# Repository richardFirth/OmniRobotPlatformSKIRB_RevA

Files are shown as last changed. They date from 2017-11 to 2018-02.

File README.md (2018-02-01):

# OmniRobotPlatformSKIRB_RevA  
Documentation of my Omni robot platform.

**work in progress, i am still adding stuff as of Jan 18**

The robot is designed to be modular and is based around a 3D Printed/Laser cut chassis.
This has a motor control board that connects to the battery and switch.
The motor control board has a socket that can accept different boards that are plugged in.

Folders:
**Chassis_Assembly**: Documentation of physical assembly of Omnibot platform

**MotorBoard_Assemly**: Documentation of motor driver Board

**XBeeControl_Module**: Documentation of a board to control the omnibot via sparkfun joystick

Different modules can be attached to the shield for control via different methods.  

**CAD Model:**  https://grabcad.com/library/omni-robot-platform-skirb_reva-1  

**Joystick Code and Case:** https://github.com/richardFirth/WirelessJoystick  

Order PCB's in Model  
**Motor Control Board:** https://oshpark.com/shared_projects/BiVYTwTP  
**XBee plugonboard** https://oshpark.com/shared_projects/E1SlzLHo  
**Xbee Board:** https://oshpark.com/shared_projects/hA4cGipD  
**MotorClip** https://oshpark.com/shared_projects/modA4HzY (Need 4)  
**MotorBackplate** https://oshpark.com/shared_projects/eEKy6Eoc (Need 4, optional)

(you need one of each to build the Robot)  

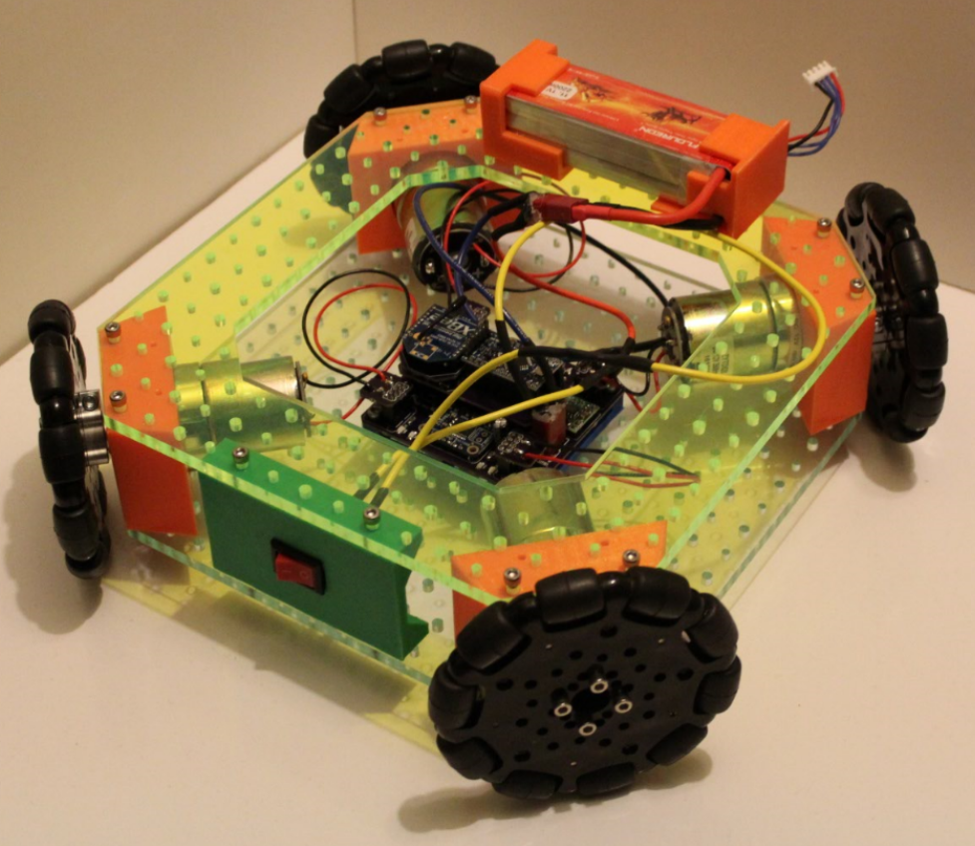
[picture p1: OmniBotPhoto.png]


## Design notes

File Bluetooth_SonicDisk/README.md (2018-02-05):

# Bluetooth Sonic Disk

This is for a version of the omnibot that uses the sonic disk https://github.com/richardFirth/sonicdisc on top of it to display the surroundings
using bluetooth.

Sonic Disk -> https://github.com/richardFirth/sonicdisc / https://platis.solutions/blog/2017/08/27/sonicdisc-360-ultrasonic-scanner/

Youtube video: https://www.youtube.com/watch?v=5h7yqy7BErE (crappy video - if there is interest I'll make a better one)

**CAD Model:**  https://grabcad.com/library/sonic-disk-mount-1   

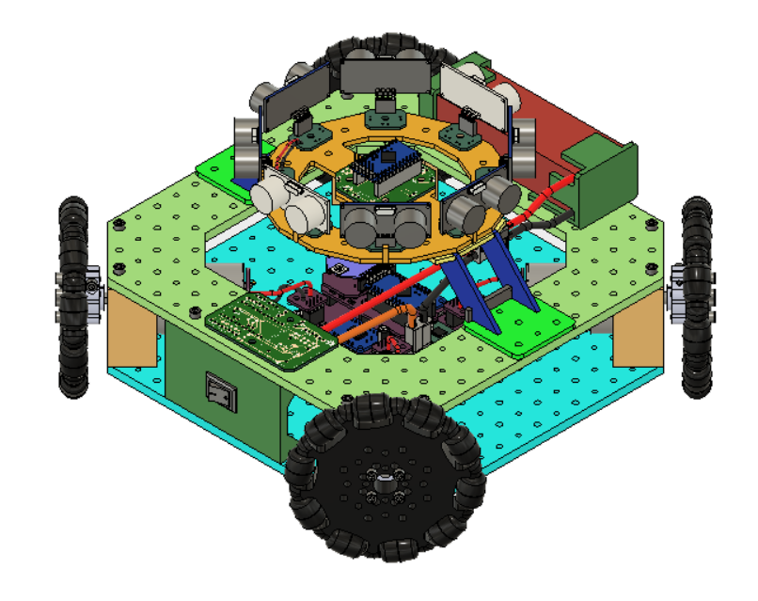
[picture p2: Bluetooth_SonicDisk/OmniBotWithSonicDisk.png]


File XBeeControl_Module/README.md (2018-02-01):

# XBeeControl_Module

Plug-In Module for control with xbee joystick 
https://github.com/richardFirth/WirelessJoystick 

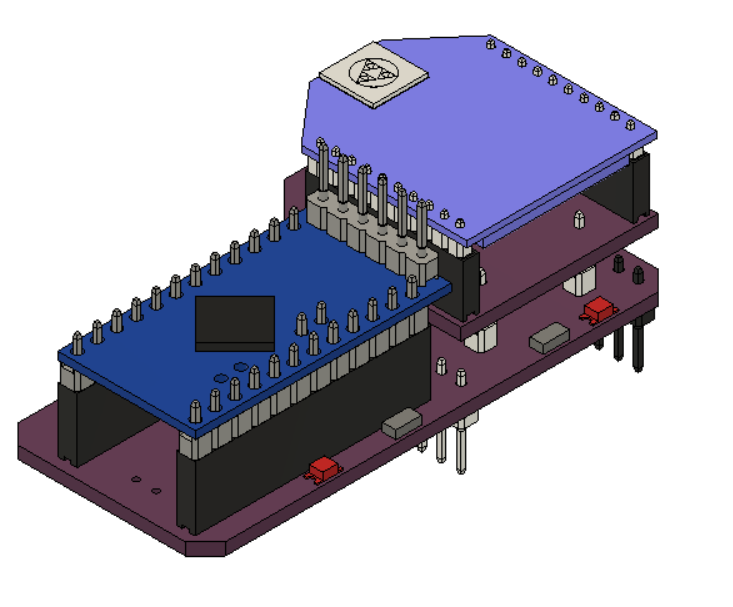
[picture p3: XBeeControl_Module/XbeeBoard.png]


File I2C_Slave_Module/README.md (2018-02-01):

# I2C Slave Module

This module has the arduino act as an I2C Slave that passes commands down to the omnibots motors.
it also exposes the power out portion of the motor board so more stuff can be attached upstream.

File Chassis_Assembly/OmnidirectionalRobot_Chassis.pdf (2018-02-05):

# Omni Robot Platform

## Richard Firth 1/25/18

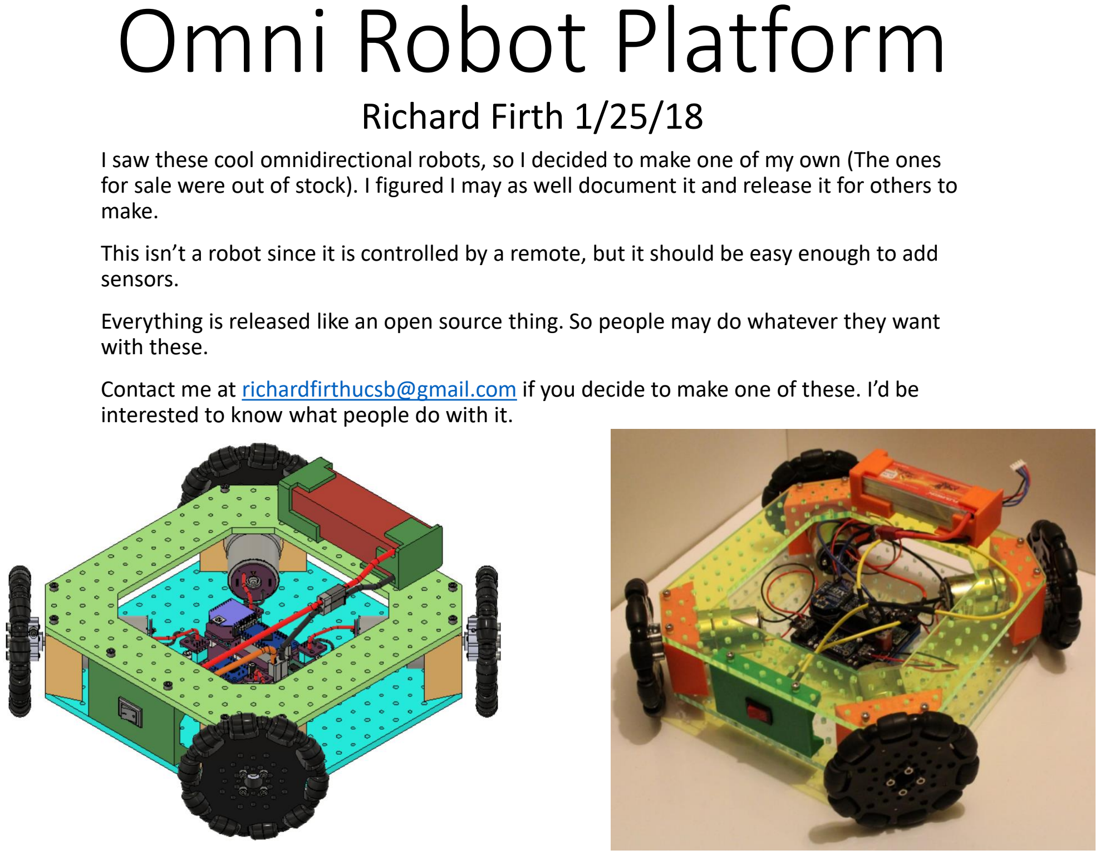
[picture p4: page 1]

I saw these cool omnidirectional robots, so I decided to make one of my own (The ones for sale were out of stock). I figured I may as well document it and release it for others to make.

This isn’t a robot since it is controlled by a remote, but it should be easy enough to add sensors.

Everything is released like an open source thing. So people may do whatever they want with these.

Contact me at richardfirthucsb@gmail.com if you decide to make one of these. I’d be interested to know what people do with it.

# Goal / Contents

- Electronics/soldering
- Arduino Programming
- Knowledge of Xbees
- 3D printing
- ~$450 + equipment

# Resources:

# Prerequisites:

Github: https://github.com/richardFirth/OmniRobotPlatformSKIRB_RevA CAD Files: https://grabcad.com/library/omni-robot-platform-skirb_reva-1

- Provide high level instructions on how to construct the robot platform
- List the parts used in constructing the robot platform
- Go over the design/engineering of the thing, so that people can understand how it was designed & constructed

# Price estimate: ~$200

# - Each wheel assy ~$30 ($120 for wheels) - LiPO battery $16 - Misc screws, wire ect $20 - 3D printed parts, laser cut parts $30

# 3D Printed Parts Index

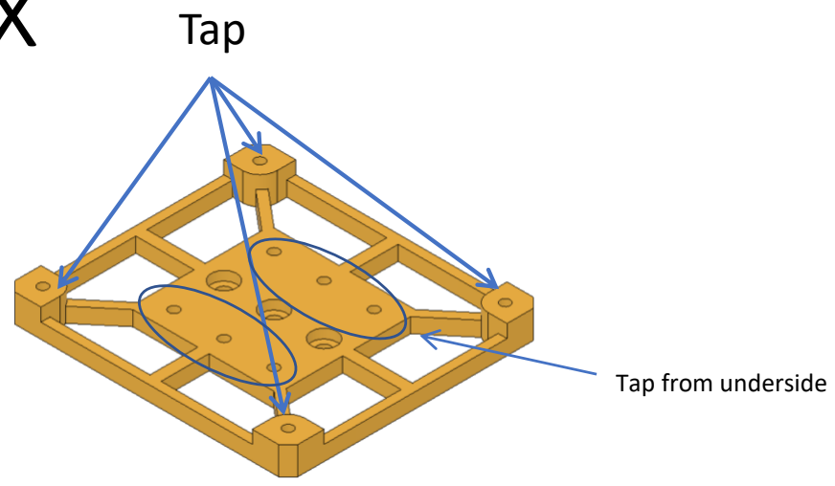
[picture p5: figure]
Tap; Tap from underside
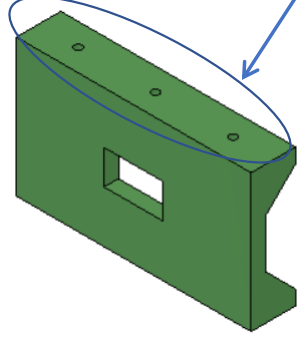
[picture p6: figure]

SwitchHolder

Standoff_Omni

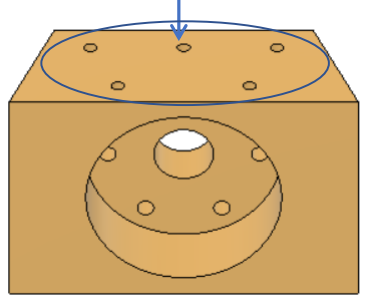
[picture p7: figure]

MotorHolderD (X4)

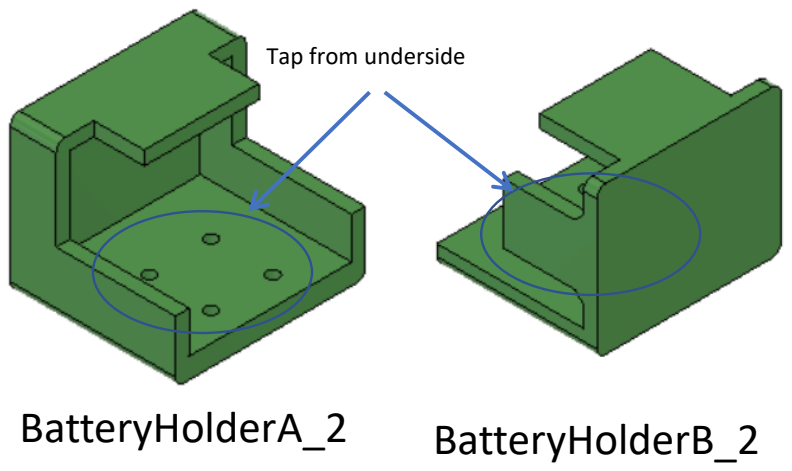
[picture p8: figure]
BatteryHolderA_2; BatteryHolderB_2; Tap from underside

- Holes match the spacing for attaching stuff bought on servocity.com
- Thread holes using a 6-32 tap
- https://www.mcmaster.com/#2548a12/=1a34129
- https://www.mcmaster.com/#27175a114/=1a340o6

Tap both top and bottom

Tap both top and bottom

# Wheels

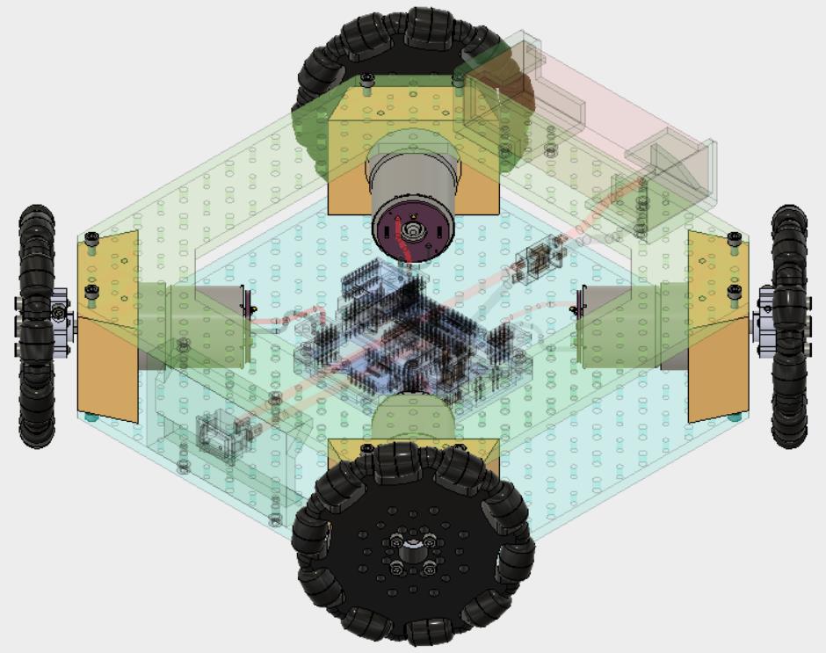
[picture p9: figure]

# Wheel Assembly (4 needed)

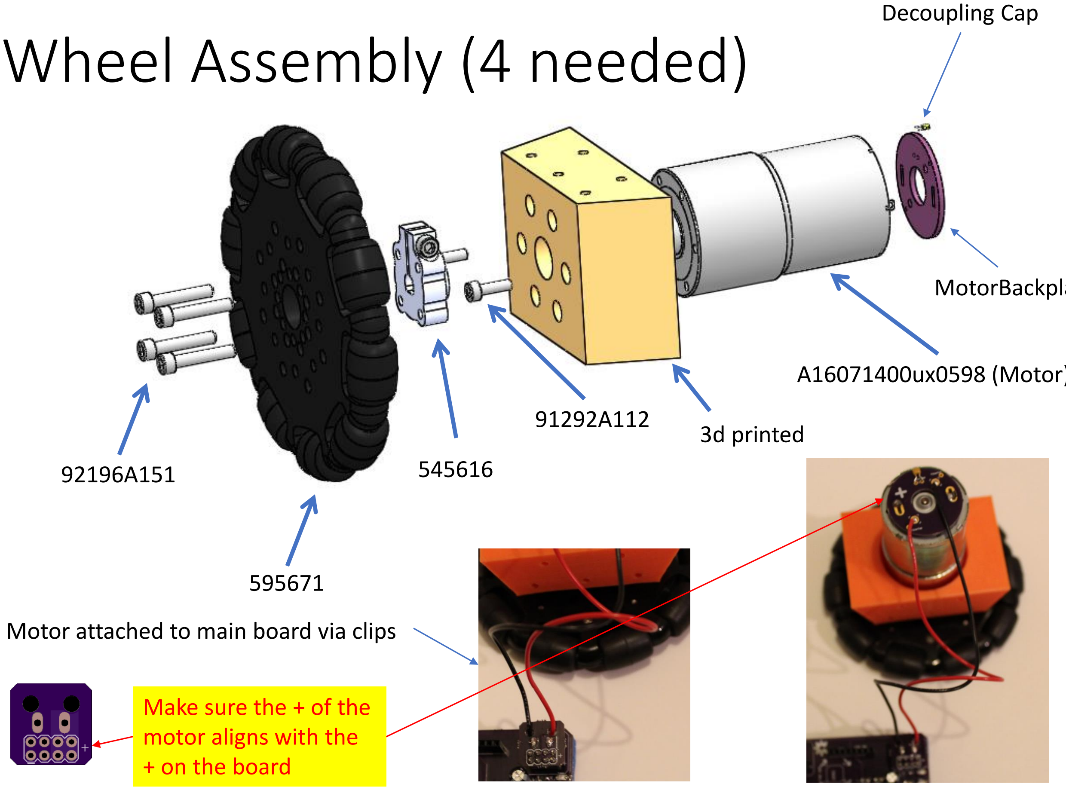
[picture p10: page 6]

A16071400ux0598 (Motor)

92196A151

91292A112

595671

545616

Decoupling Cap

Motor attached to main board via clips

3d printed

MotorBackplate

Make sure the + of the
motor aligns with the
+ on the board

Part # | Part | Pic | Source
92196A151 | 18-8 Stainless Steel Socket Head Screw 6-32 Thread Size, 3/4" Long | | https://www.mcmaster.com/#92196A151/
92196A146 | 18-8 Stainless Steel Socket Head Screw, 6-32 Thread Size, 3/8" Long | | https://www.mcmaster.com/#92196A146/
91292A112 | 8-8 Stainless Steel Socket Head Screw M3 x 0.5 mm Thread, 8 mm Long | | https://www.mcmaster.com/#91292A112/
Part # | Description | Pic | Source
ZGA37RG31 (Gearbox) a16071400ux0598 (Uxcell P/N) | 12V 100 RPM DC Motor | | https://www.amazon.com/gp/product/B01KTZXZ1G/
545616 | Face Tapped Clamping Hubs, 0.770" Pattern (6mm) | | https://www.servocity.com/770-clamping-hubs#348=98
595671 | 4" Omni Wheel | | https://www.servocity.com/4-omni-wheel
0.1 uF Ceramic Capacitor | 0.1 uF Ceramic Capacitor | | https://www.amazon.com/gp/product/B01N3L8IE1
MotorBackplate | MotorBackplate | | https://oshpark.com/shared_projects/eEKy6Eoc
MotorClip | MotorClip | | https://oshpark.com/shared_projects/modA4HzY
Wire | Wire | | https://www.amazon.com/gp/product/B01180QKJ0/

# Bill of materials – Wheel Assemblies (Need 4)

# Body

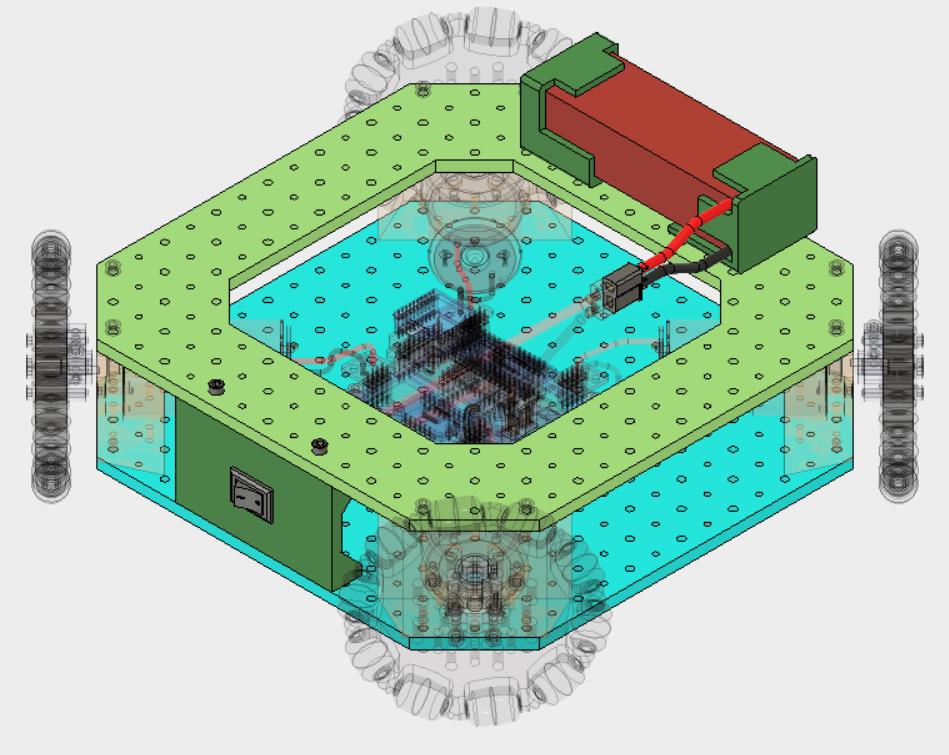
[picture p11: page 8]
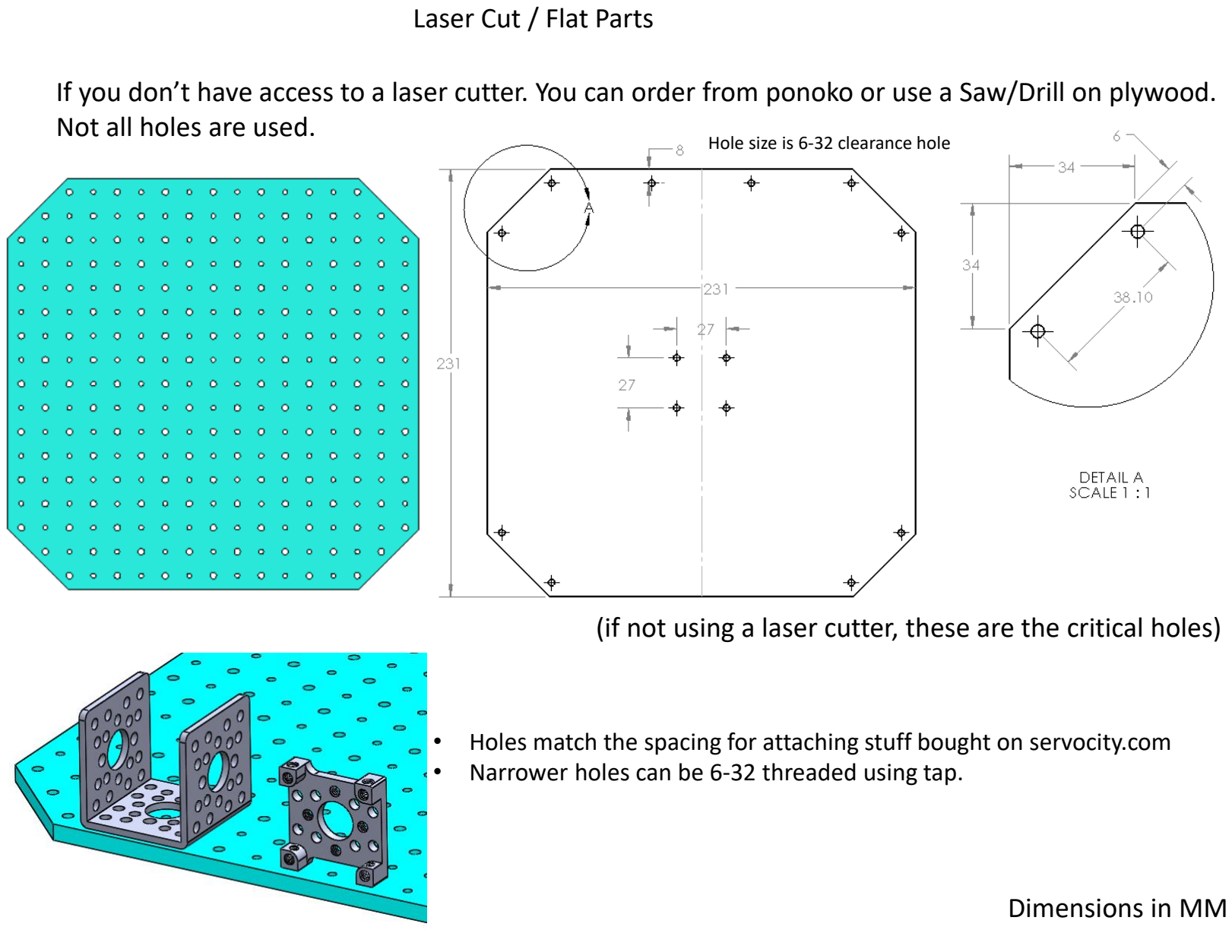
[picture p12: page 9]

Laser Cut / Flat Parts

If you don’t have access to a laser cutter. You can order from ponoko or use a Saw/Drill on plywood. Not all holes are used.

Dimensions in MM

(if not using a laser cutter, these are the critical holes)

Hole size is 6-32 clearance hole

- Holes match the spacing for attaching stuff bought on servocity.com
- Narrower holes can be 6-32 threaded using tap.

If you don’t have access to a laser cutter. You can order from ponoko or use a Saw/Drill on plywood. Extra holes are to support future stuff you might add.

Laser Cut / Flat Parts

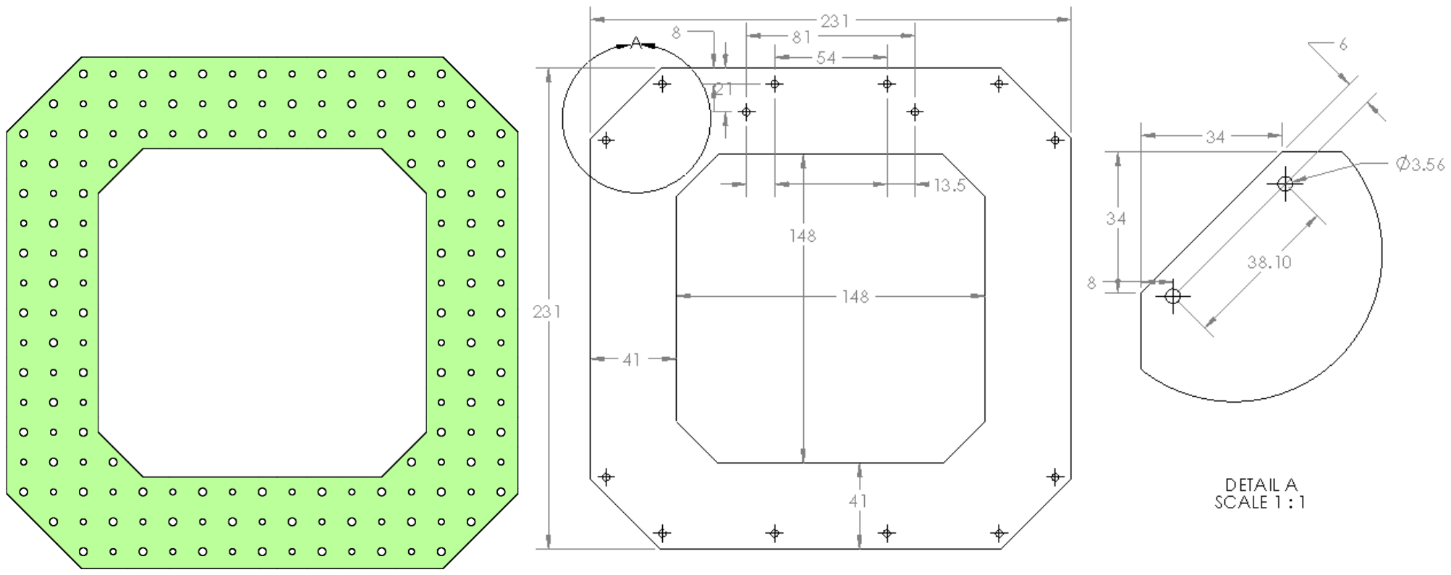
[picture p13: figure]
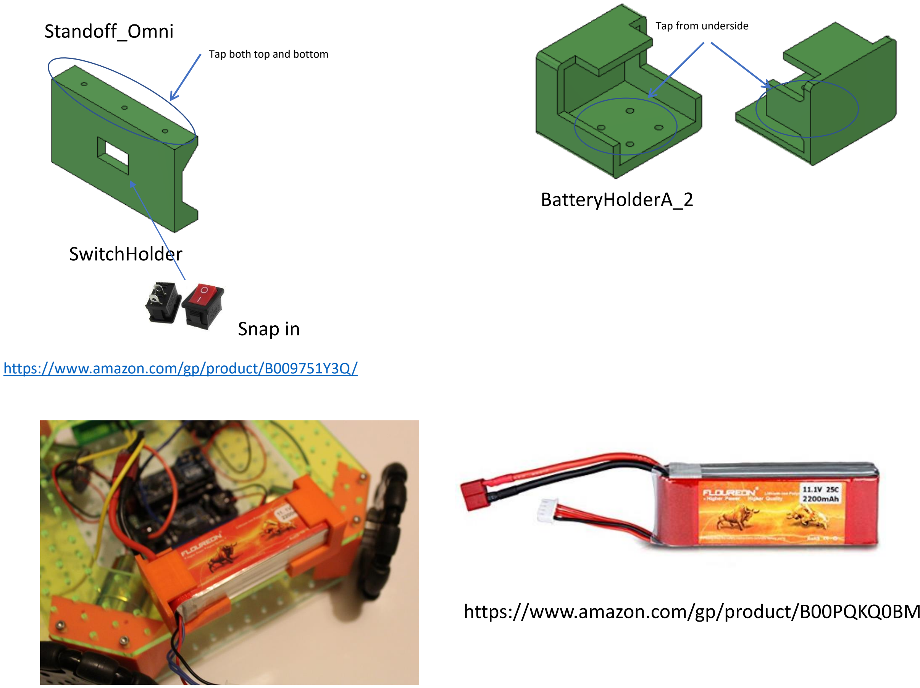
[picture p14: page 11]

SwitchHolder

Standoff_Omni

Tap both top and bottom

https://www.amazon.com/gp/product/B00PQKQ0BM

BatteryHolderA_2

Tap from underside

https://www.amazon.com/gp/product/B009751Y3Q/

Snap in

Wiring

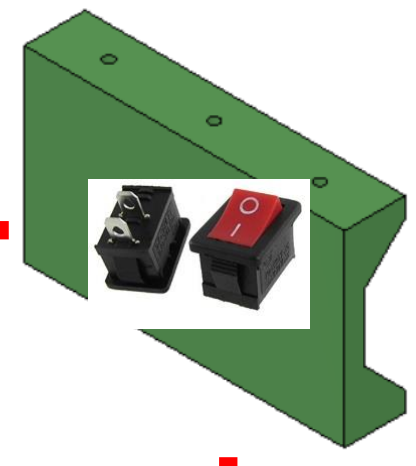
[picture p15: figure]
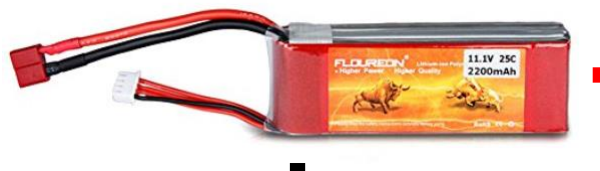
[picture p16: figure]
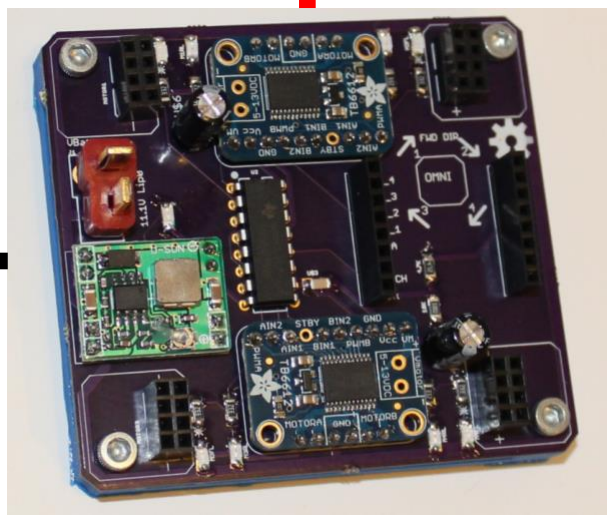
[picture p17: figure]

# Circuit board Holder

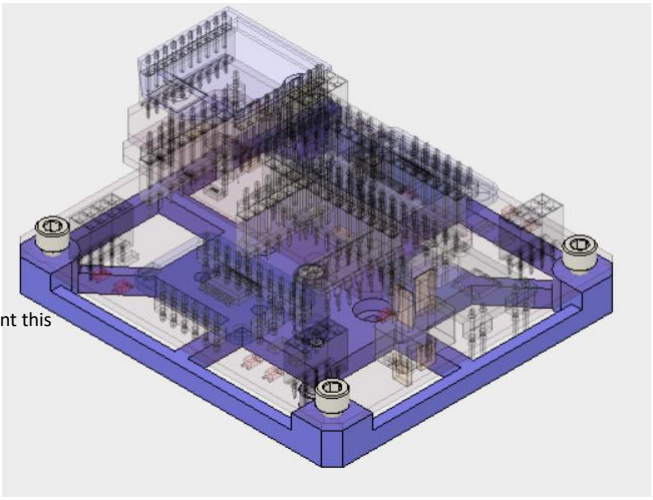
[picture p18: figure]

3d Print this

MotorClip -> https://oshpark.com/shared_projects/modA4HzY (need 4)
MotorBackplate -> https://oshpark.com/shared_projects/eEKy6Eoc (need 4, optional part)

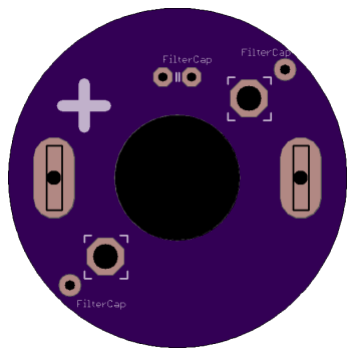
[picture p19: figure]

MotorBackplate

Not to Scale!

MotorClip

# Printed Circuit Boards

# Design Notes - Mechanical

- For the frame and wheels, the materials were chosen based on the fact I have access to a laser cutter and 3D printer and am familiar with them
- Wheels, hubs, screw sizes ect were chosen to match stuff off ServoCity, because I have a bunch of their stuff already, and the hole pattern lets me attach actobotics stuff to the robot
- The motor was the first guess, and worked so I didn’t try others. Of the choices available 100 RPM seemed a good place to start. (https://www.amazon.com/gp/product/B01KTZXZ1G/) and they don’t use a lot of current (around 0.5 amp when resisted according to an ad hoc test – I used a benchtop power supply and grabbed the wheel physically and resisted it while looking at the current)
- The battery was the second of a two pack bought for another project, but works well here.
- I didn’t really think about cost as a thing since this is a one off for learning purposes

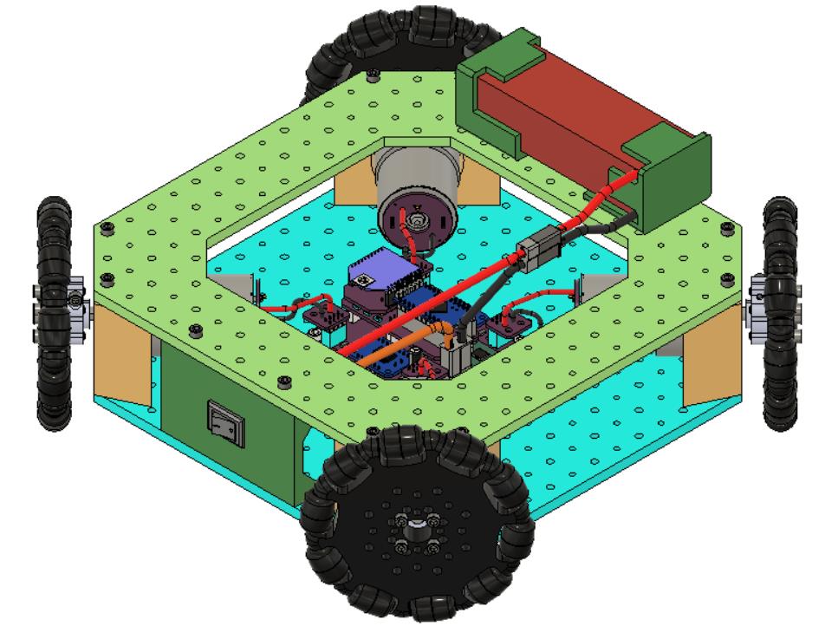
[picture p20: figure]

Forward sense of each motor should cause clockwise rotation of robot (VCC to + of motor, GND to -)

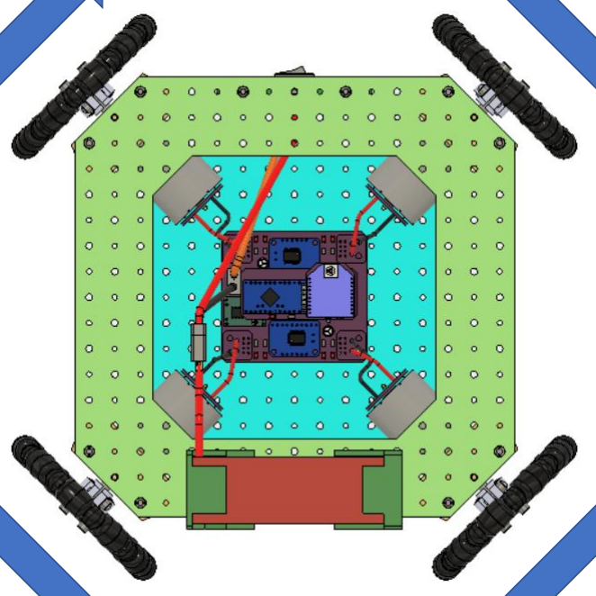
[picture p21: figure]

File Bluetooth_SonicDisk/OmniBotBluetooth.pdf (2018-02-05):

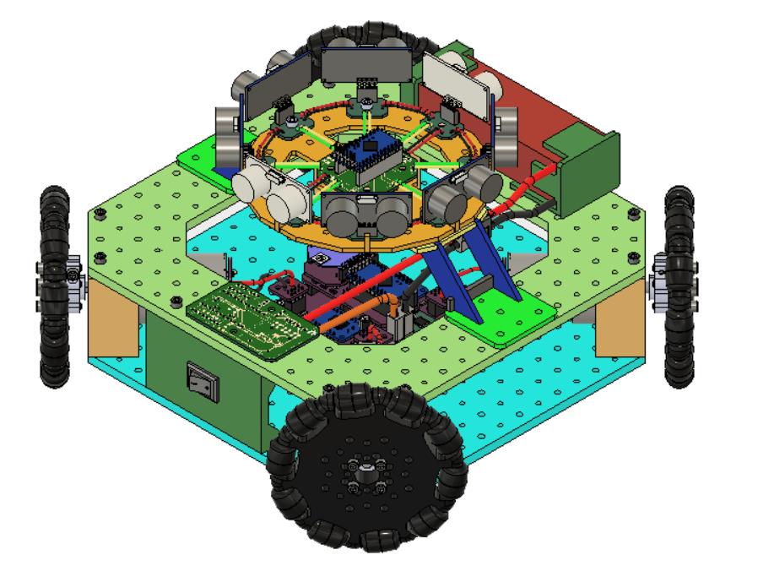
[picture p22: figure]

Uses Three Arduino pro minis.

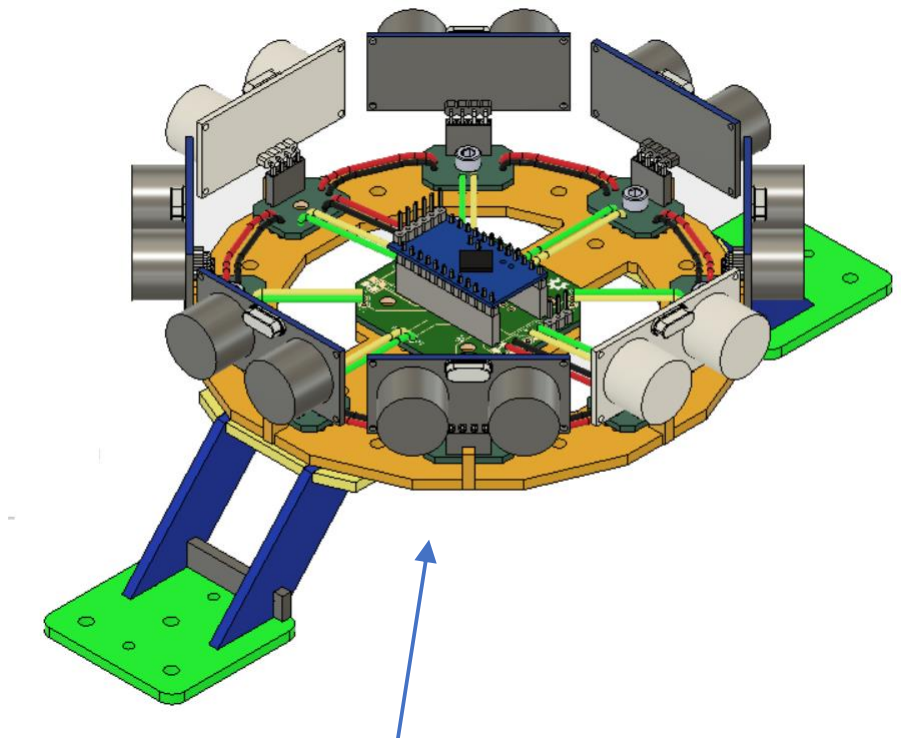
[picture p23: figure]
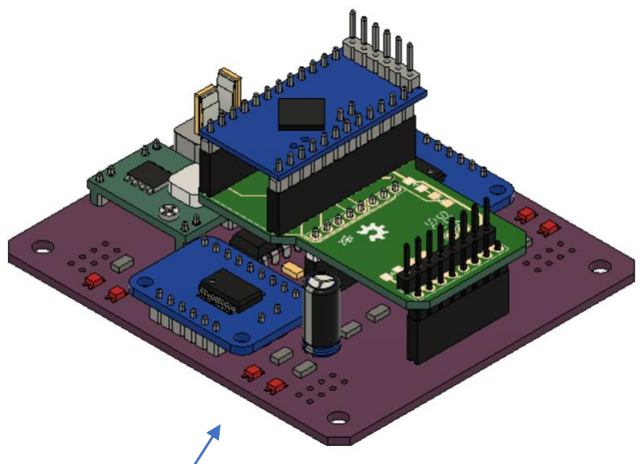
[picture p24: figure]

Arduino 2 – Sonic Disc
Code:
https://github.com/richardFirth/sonicdisc/tree/master/firmware/SonicDisc (is same as https://github.com/platisd/sonicdisc/tree/master/firmware )

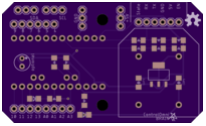
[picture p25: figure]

Arduino 1 – Sonic Disc
Code:
https://github.com/richardFirth/OmniRobotPlatformSKIRB_RevA/tree/master/Bluetooth_SonicDisk/BrainMaster (https://github.com/richardFirth/OmniRobotPlatformSKIRB_RevA/tree/master/Bluetooth_SonicDisk/BrainMaster)

Arduino 3 – Motor Board
Code:
https://github.com/richardFirth/OmniRobotPlatformSKIRB_RevA/tree/master/I2C_Slave_Module/OmniwheelRobot_I2CSlave (https://github.com/richardFirth/OmniRobotPlatformSKIRB_RevA/tree/master/I2C_Slave_Module/OmniwheelRobot_I2CSlave)


## SDA SCL


## SDA SCL

## PIN 2


## INT PIN

## Power & GND

## Power & GND

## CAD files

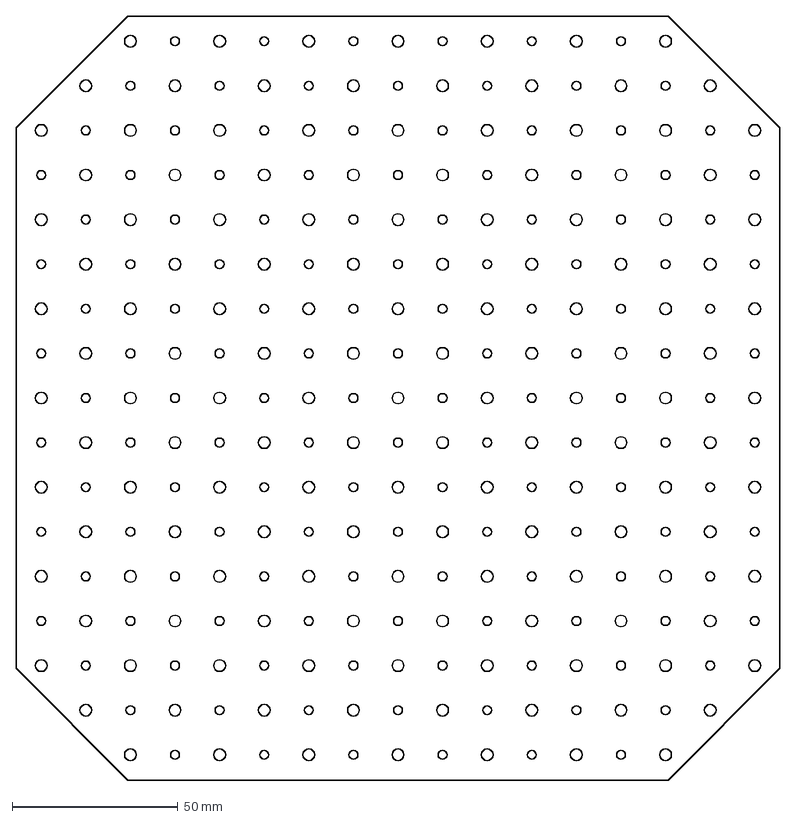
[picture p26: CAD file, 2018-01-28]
Chassis_Assembly/DXF/LowerPlate.dxf
230.8 x 230.8 mm

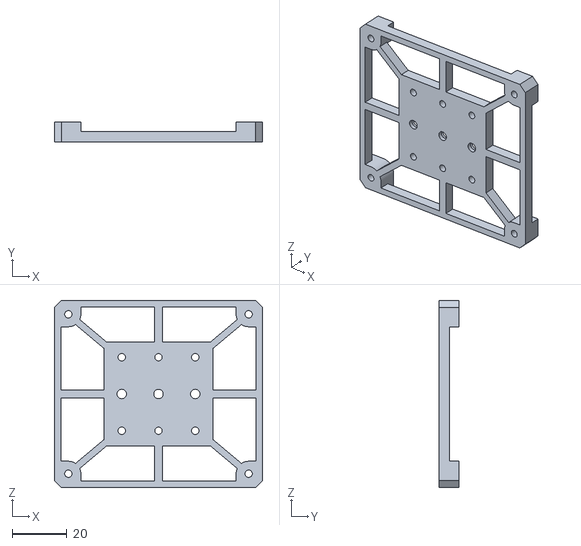
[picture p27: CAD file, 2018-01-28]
Chassis_Assembly/STL/PCB_Holder.stl
76.2 x 7.50 x 68.6

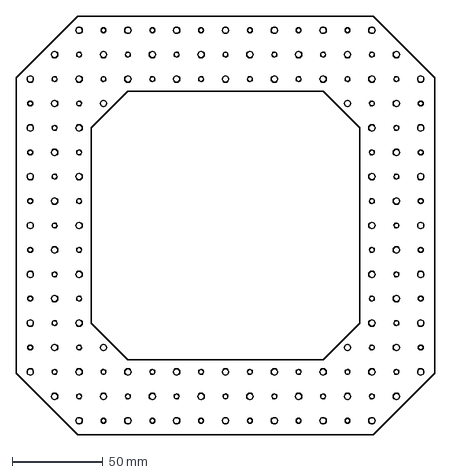
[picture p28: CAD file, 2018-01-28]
Chassis_Assembly/DXF/UpperPlate.dxf
230.8 x 230.8 mm

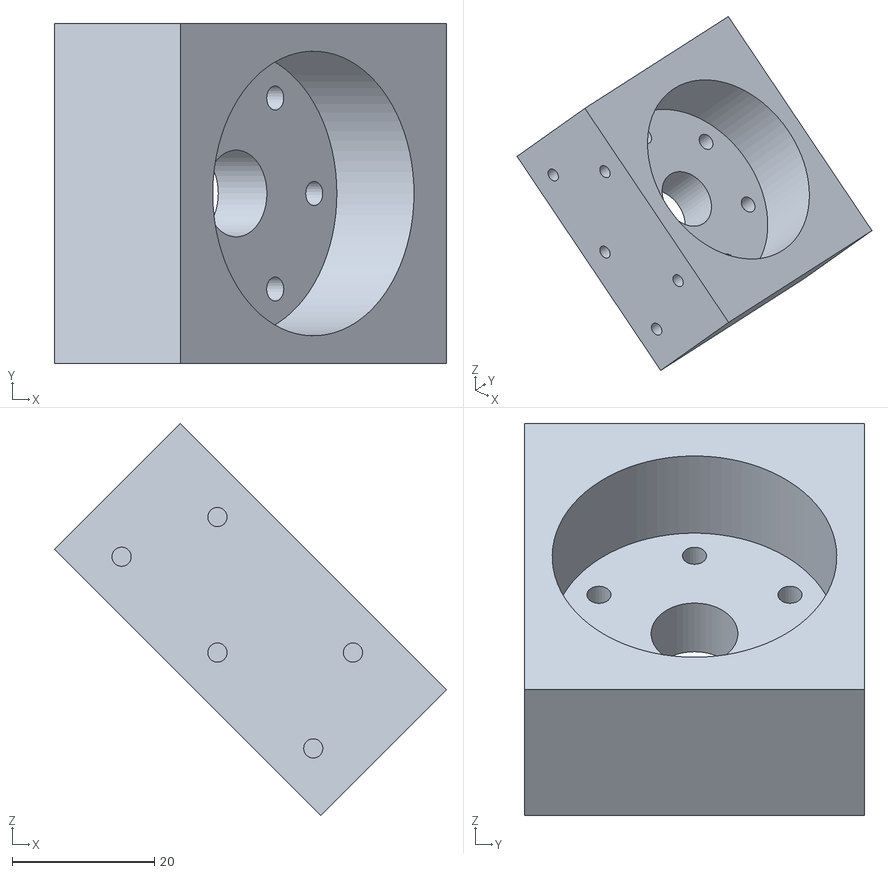
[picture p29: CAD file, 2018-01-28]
Chassis_Assembly/STL/MotorHolderE.stl
55.1 x 47.8 x 55.1

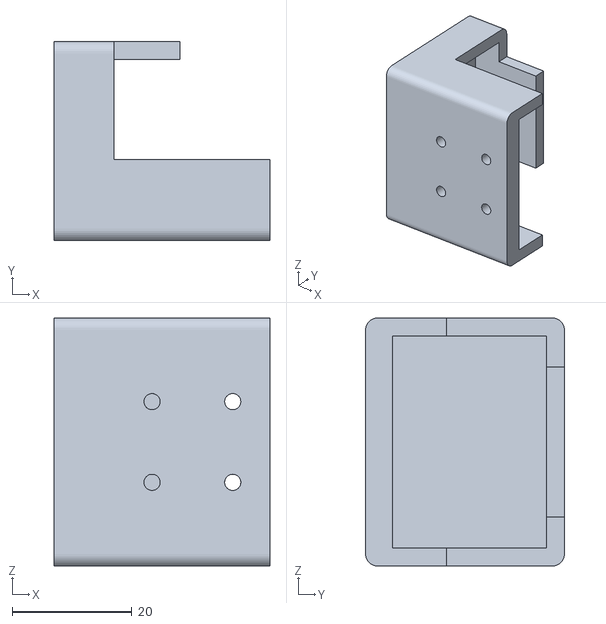
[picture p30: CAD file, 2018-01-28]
Chassis_Assembly/STL/BatteryHolderA_2.stl
36.0 x 33.2 x 41.4

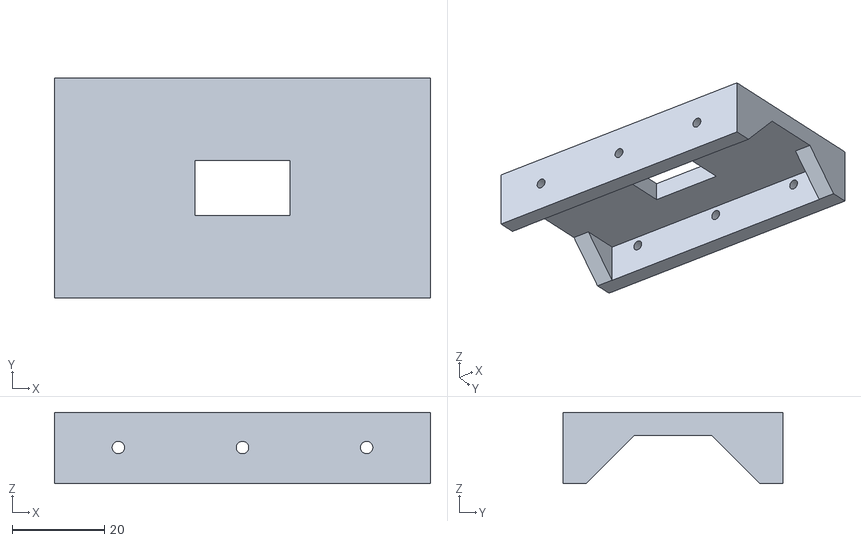
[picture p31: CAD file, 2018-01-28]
Chassis_Assembly/STL/SwitchHolder.stl
81.6 x 47.8 x 15.4

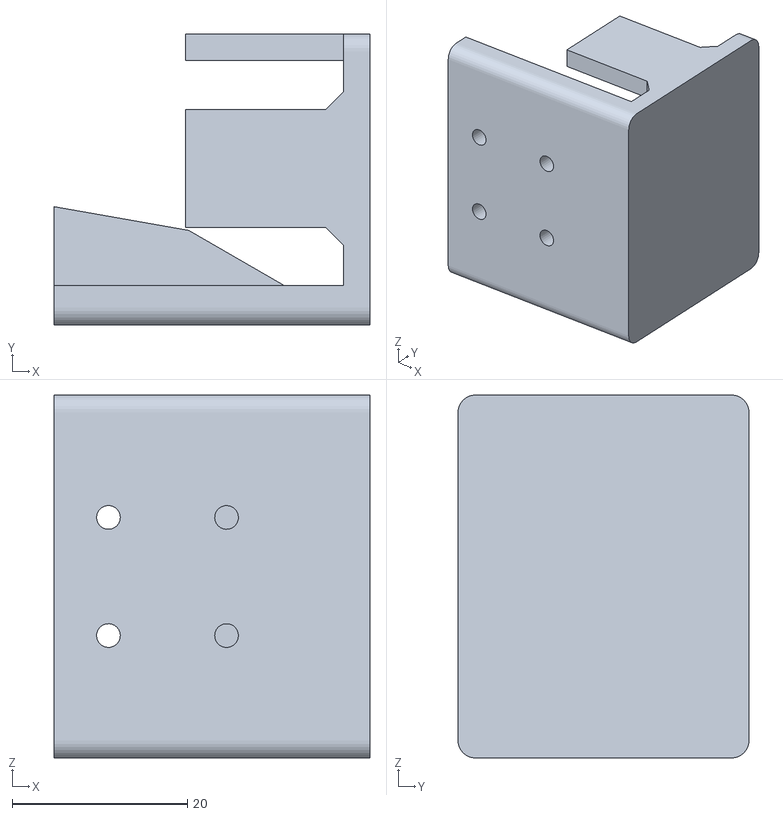
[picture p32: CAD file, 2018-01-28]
Chassis_Assembly/STL/BatteryHolderB_2.stl
36.0 x 33.2 x 41.4

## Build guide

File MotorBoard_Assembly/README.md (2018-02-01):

# Motor Board

Instructions for assembling the motor board.
This is used by each of the modules to control the motors of the omnibot.
It has a common output that can be used by whatever you put above it.

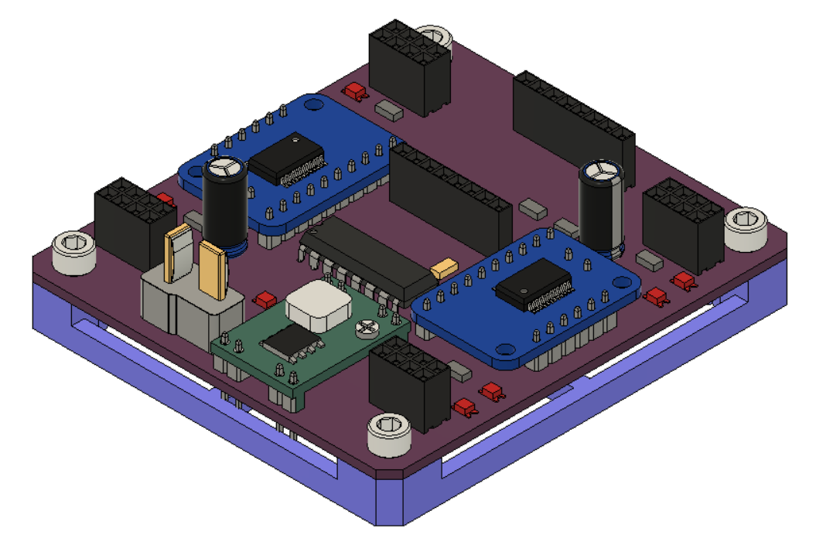
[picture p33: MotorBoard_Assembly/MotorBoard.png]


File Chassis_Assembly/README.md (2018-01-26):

# Chassis Construction  

instructions for construction of physical chassis.
Uses laser cut & 3D Printed components. 

**CAD Model:**  https://grabcad.com/library/omni-robot-platform-skirb_reva-1

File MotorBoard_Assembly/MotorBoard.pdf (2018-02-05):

# Omni Robot Platform

## Richard Firth 11/25/17

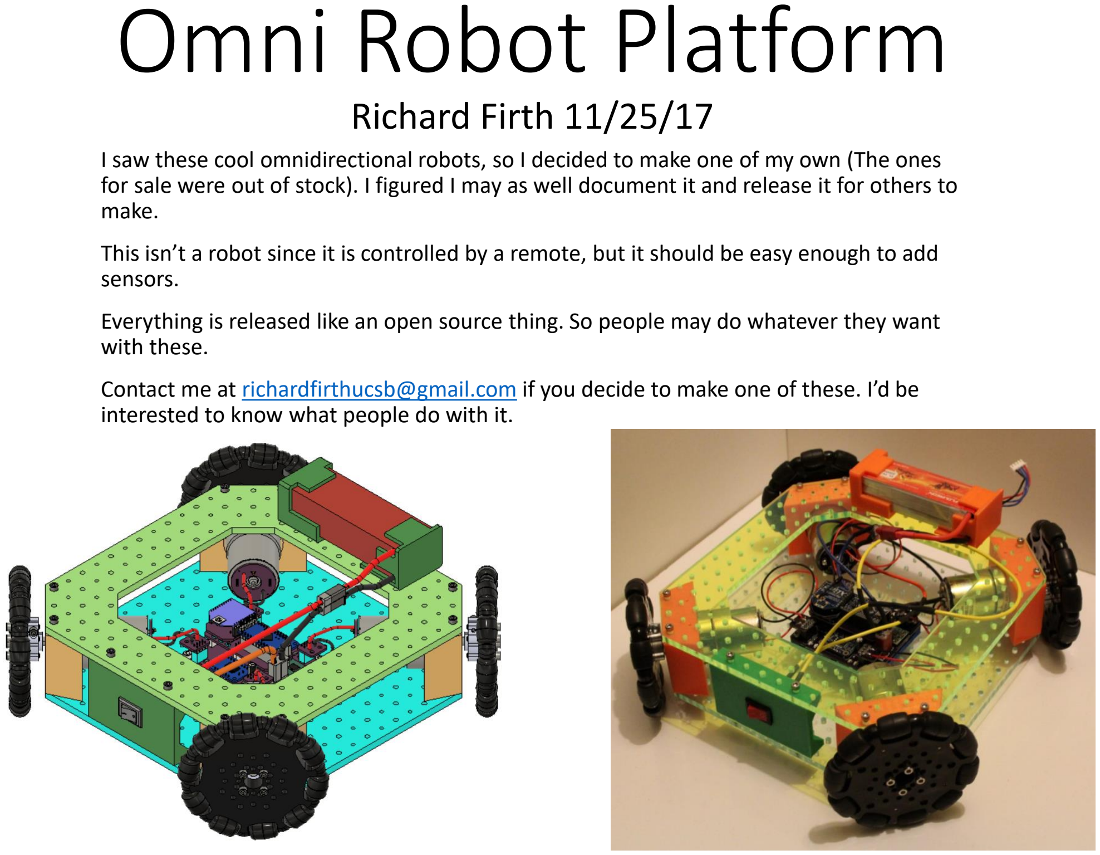
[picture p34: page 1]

I saw these cool omnidirectional robots, so I decided to make one of my own (The ones for sale were out of stock). I figured I may as well document it and release it for others to make.

This isn’t a robot since it is controlled by a remote, but it should be easy enough to add sensors.

Everything is released like an open source thing. So people may do whatever they want with these.

Contact me at richardfirthucsb@gmail.com if you decide to make one of these. I’d be interested to know what people do with it.

# Goal / Contents

- Electronics/soldering
- Arduino Programming

# Resources:

# Prerequisites:

Github: https://github.com/richardFirth/OmniRobotPlatformSKIRB_RevA CAD Files: https://grabcad.com/library/omni-robot-platform-skirb_reva-1

- Provide high level instructions on how to construct the robot platform
- List the parts used in constructing the robot platform
- Go over the design/engineering of the thing, so that people can understand how it was designed & constructed

# Motor control board

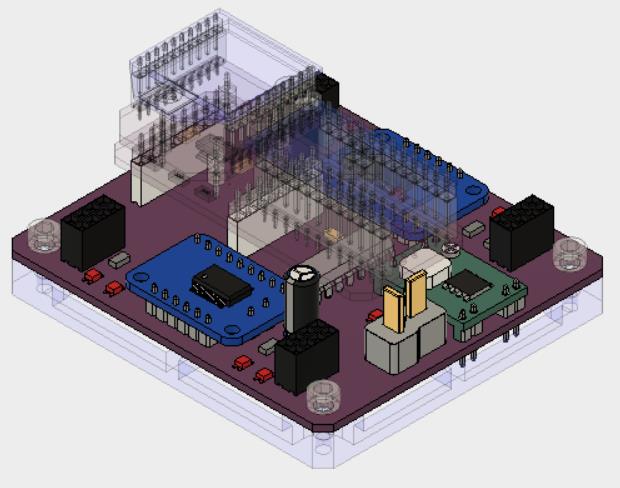
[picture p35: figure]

# OmniMotor_MotorOnly Assembly

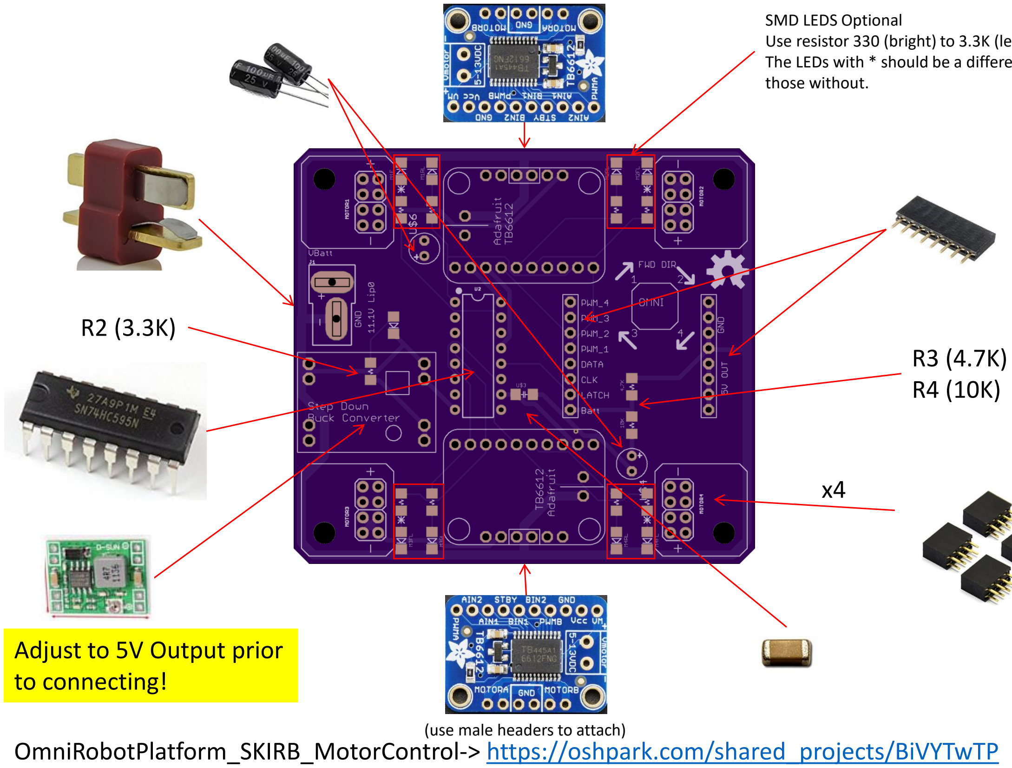
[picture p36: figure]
SMD LEDS Optional; those without.; (use male headers to attach); Adjust to 5V Output prior to connecting!; OmniRobotPlatform_SKIRB_MotorControl-> https://oshpark.com/shared_projects/BiVYTwTP

Use resistor 330 (bright) to 3.3K (less bright) The LEDs with * should be a different color to

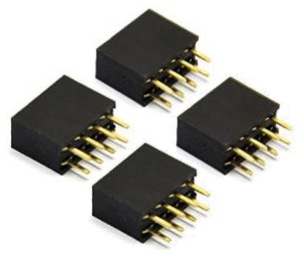
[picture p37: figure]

# OmniMotor_MotorOnly Assembly

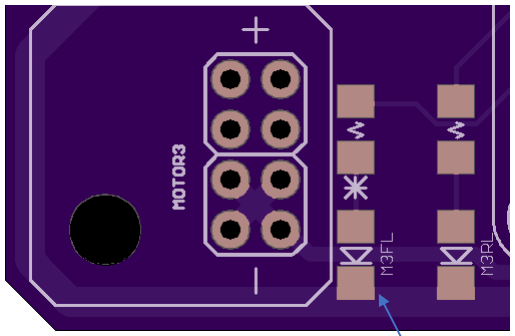
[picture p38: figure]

If you add the SMD LEDS, make the ones with the * all the same color, and the other ones a different color. These indicate ‘forwards’ and ‘backwards’ Use 3.3K resisitors for the SMD LEDS.

# OmniMotor_MotorOnly Assembly

MOTOR 1 | MOTOR 2
MOTOR 3 | MOTOR 4

Part # | Part | Pic | Source
1 | SN74HC595 Shift Register | | https://www.amazon.com/gp/product/B011NA30RK
2 | Adafruit TB6612 1.2A DC/Stepper Motor Driver Breakout Board | | https://www.adafruit.com/product/2448
3 | Icstation Mini DC Voltage Regulator Step Down Buck Converter Power Supply Module 4.5V-28V to 0.8V-20V 3A | | https://www.amazon.com/gp/product/B06Y1ZBY8Q
4 | Plug Connectors Deans Style | | https://www.amazon.com/gp/product/B00S7G4A14
5 | 2.54mm Pitch 2X4 8 Pin Female Double Row Straight Header PCB Connector | | https://www.amazon.com/gp/product/B01IHBCO2K
6 | 100 uF 25 V 612 Electrolytic capacitor | | https://www.amazon.com/gp/product/B01M8QC1E3
7 | 2.54mm Single Row Female Pitch Header Socket Connector PCB 8 Pin Strip | | https://www.amazon.com/gp/product/B00SUXT67M
8 | AVX 0.1uF 50V SMD (Surface Mount) | | https://www.amazon.com/gp/product/B0015A6Z5I
Part Num | Resistor Values (1206 SMT) | Link
R1 | 330 Ohm | https://www.amazon.com/gp/product/B00NQ4JZDA
R2 | 3.3K Ohm | https://www.amazon.com/gp/product/B007V6AQ64
R3 | 4.7K Ohm | https://www.amazon.com/gp/product/B01DKC5BBM
R4 | 10K Ohm | https://www.amazon.com/gp/product/B073RYS2BL

# OmniMotor_MotorOnly BOM

OmniRobotPlatform_SKIRB_MotorControl-> https://oshpark.com/shared_projects/BiVYTwTP

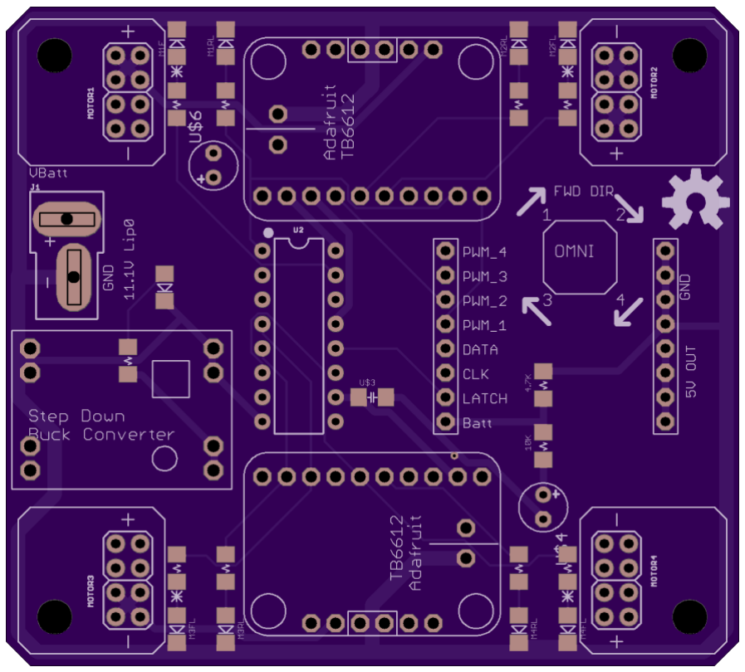
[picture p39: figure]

OmniRobotPlatform_SKIRB_MotorControl

Not to Scale!

# Printed Circuit Boards

# Design Notes - Electrical

- The motor portion was separated from the control portion, since I figured I would be adding sensors and redoing the control portion later
- Shift register used to control the motor drivers, which lets me use 3 pins to control 8 inputs.
- I used the 2X4 female headers at little clips for the motors so it’s easy to attach and detach them.
- SMD lights are there because I just learned to do SMD stuff and wanted to put them everywhere and see stuff.

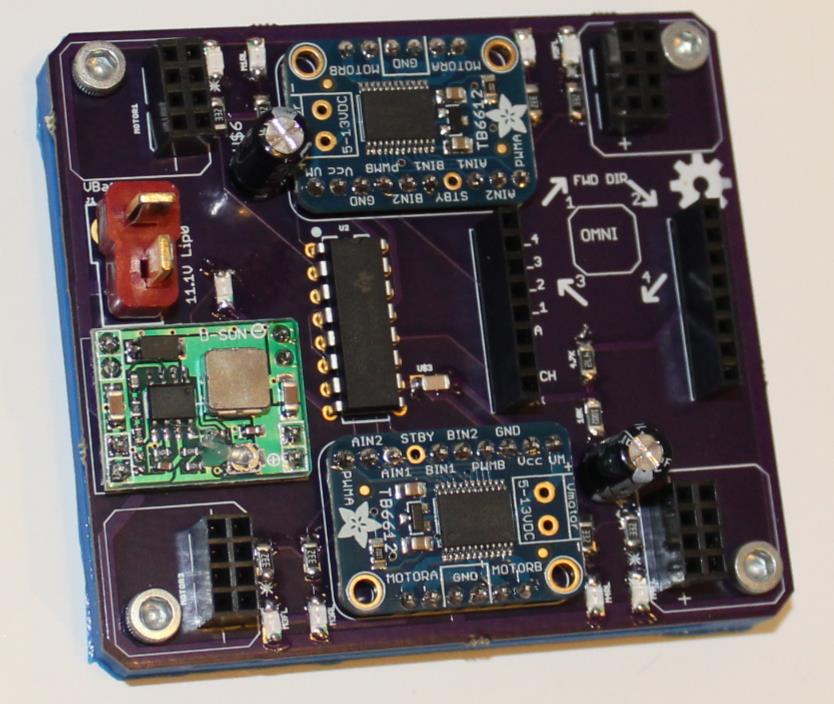
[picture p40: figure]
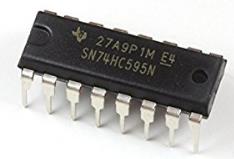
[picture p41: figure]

# Design Notes - Electrical

4 pins connect to ground

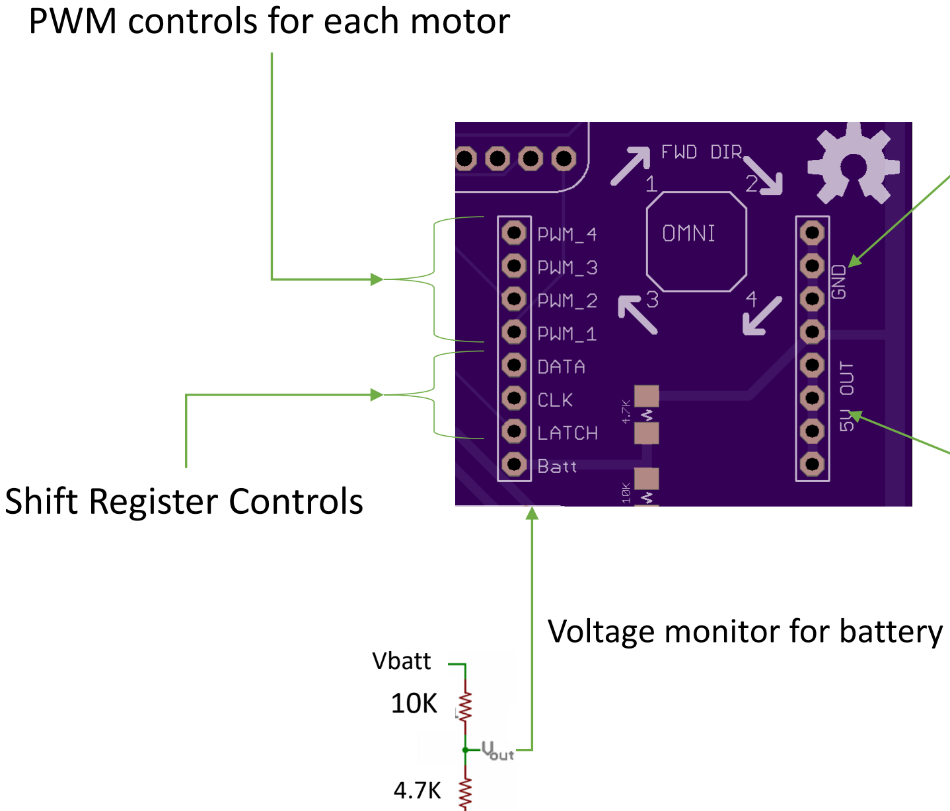
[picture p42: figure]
PWM controls for each motor; Shift Register Controls; Vbatt 10K; Voltage monitor for battery

4 pins connect to 5V from
regulator

These two rows of header pins allow modules with different microcontrollers to attach to the motor board.

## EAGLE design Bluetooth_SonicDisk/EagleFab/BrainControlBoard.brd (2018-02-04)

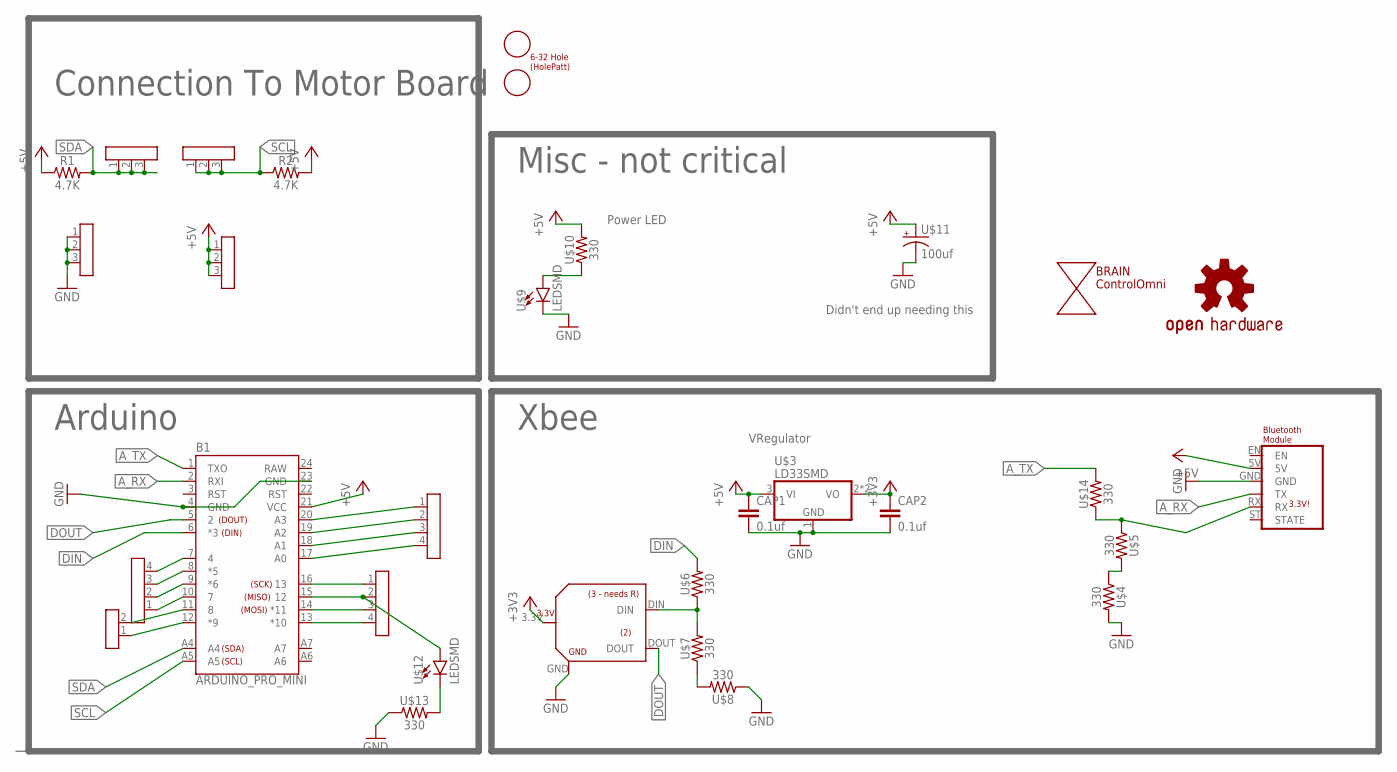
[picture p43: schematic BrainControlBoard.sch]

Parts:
B1: ARDUINO_PRO_MINI
BRAIN: ControlOmni; ANNOTATION
CAP1, CAP2: 0.1uf; C1206
LOGO1: OSHW-LOGOM; OSHW-LOGO-M
R1, R2: 4.7K; R1206
U$1: BLUETOOTH
U$2: XBEE_BOUT
U$3: LD33SMD; SOT223
U$4, U$5, U$6, U$7, U$8, U$10, U$13, U$14: 330; R1206
U$9, U$12: LEDSMD; LED_SMD
U$11: 100uf; CAP_E
U$15, U$16, U$17, U$18: 3XHEADER
U$19, U$20, U$22: 4XHEADER
U$21: 2XHEADER
U$23: 632X2

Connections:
+3V3: CAP2.1, U$2.3.3V, U$3.2 (VO), U$3.4 (VO)
+5V: B1.21 (VCC), CAP1.1, R1.1, R2.2, U$1.5V, U$3.3 (VI), U$10.2, U$11.+, U$16.1, U$16.2, U$16.3
A0: B1.17 (A0), U$19.4
A1: B1.18 (A1), U$19.3
A2: B1.19 (A2), U$19.2
A3: B1.20 (A3), U$19.1
A_RX: B1.2 (RXI), U$1.TX
A_TX: B1.1 (TXO), U$14.2
DIN: B1.6 (*3), U$6.2
DOUT: B1.5 (2), U$2.DOUT
GND: B1.4 (GND), B1.23 (GND), CAP1.2, CAP2.2, U$1.GND, U$2.GND, U$3.1 (GND), U$4.2, U$8.1, U$9.C, U$11.-, U$13.1, U$15.1, U$15.2, U$15.3
unnamed: U$9.A, U$10.1
unnamed: U$7.1, U$8.2
unnamed: U$2.DIN, U$6.1, U$7.2
unnamed: U$12.C, U$13.2
unnamed: U$4.1, U$5.2
unnamed: U$1.RX, U$5.1, U$14.1
P4: B1.7 (4), U$20.4
P5: B1.8 (*5), U$20.3
P6: B1.9 (*6), U$20.2
P7: B1.10 (7), U$20.1
P8: B1.11 (8), U$21.2
P9: B1.12 (*9), U$21.1
P10: B1.13 (*10), U$22.4
P11: B1.14 (*11), U$22.3
P12: B1.15 (12), U$12.A, U$22.2
P13: B1.16 (13), U$22.1
RAW: B1.24 (RAW)
SCL: B1.A5, R2.1, U$18.1, U$18.2, U$18.3
SDA: B1.A4, R1.2, U$17.1, U$17.2, U$17.3

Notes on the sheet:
Arduino
Xbee
VRegulator
Connection To Motor Board
Misc - not critical
Didn't end up needing this
Power LED

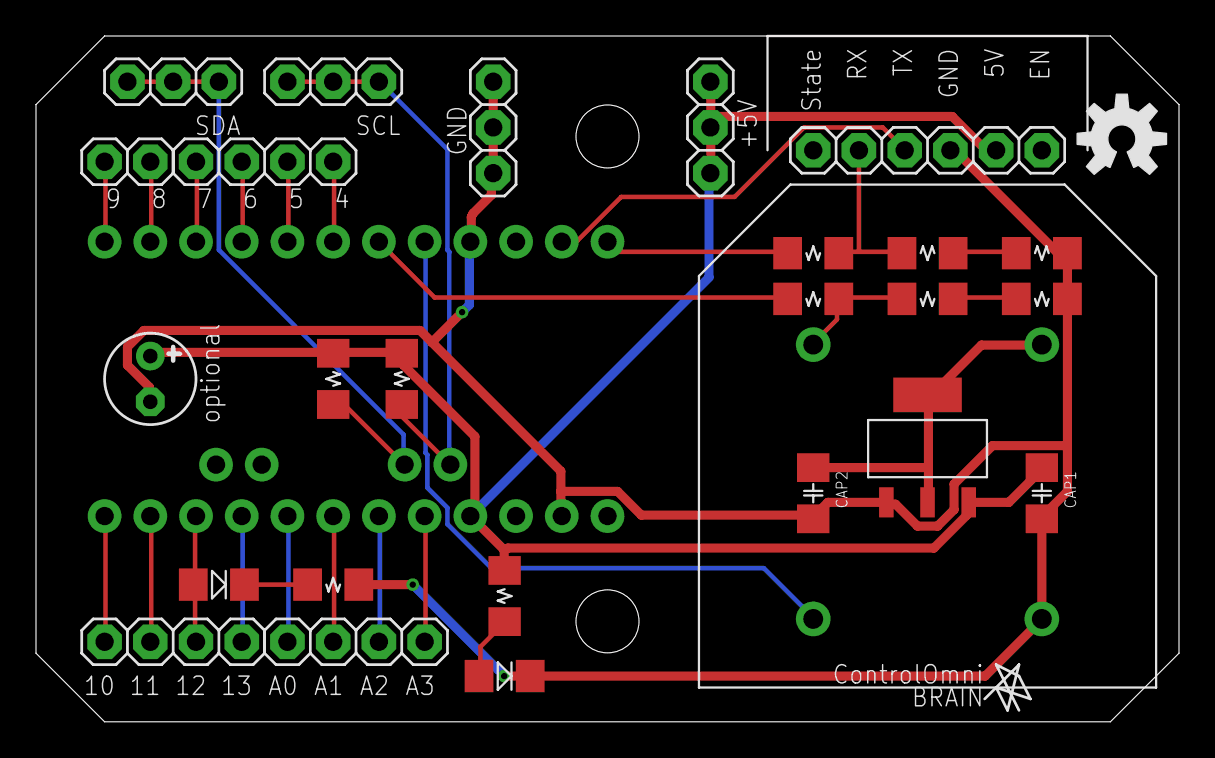
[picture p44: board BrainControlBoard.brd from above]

Board: 2 copper layers, 63.5 x 38.1 mm, 30 parts (0 on the bottom side), 29 nets.

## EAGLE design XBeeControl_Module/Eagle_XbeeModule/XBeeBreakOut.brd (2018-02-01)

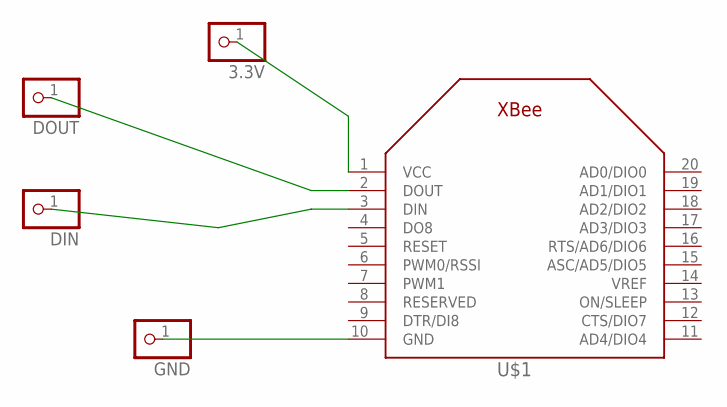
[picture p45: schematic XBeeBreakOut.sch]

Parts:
3.3V: PINHD-1X1; 1X01
DIN: PINHD-1X1; 1X01
DOUT: PINHD-1X1; 1X01
GND: PINHD-1X1; 1X01
U$1: XBEE

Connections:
DIN: DIN.1, U$1.3 (DIN)
DOUT: DOUT.1, U$1.2 (DOUT)
GND: GND.1, U$1.10 (GND)
VCC: 3.3V.1, U$1.1 (VCC)

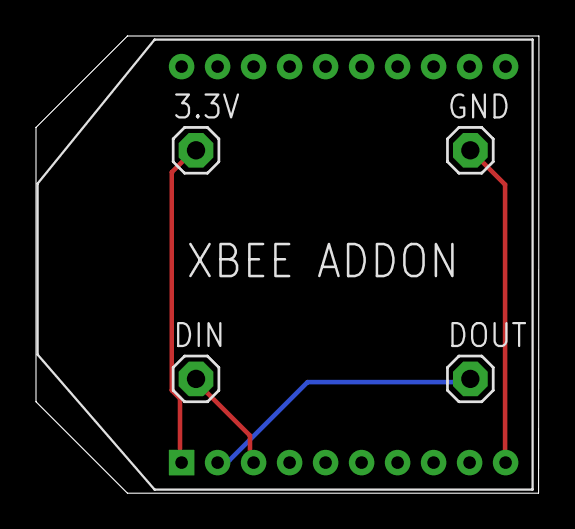
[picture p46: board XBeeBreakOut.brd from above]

Board: 2 copper layers, 27.9 x 25.4 mm, 5 parts (0 on the bottom side), 4 nets.

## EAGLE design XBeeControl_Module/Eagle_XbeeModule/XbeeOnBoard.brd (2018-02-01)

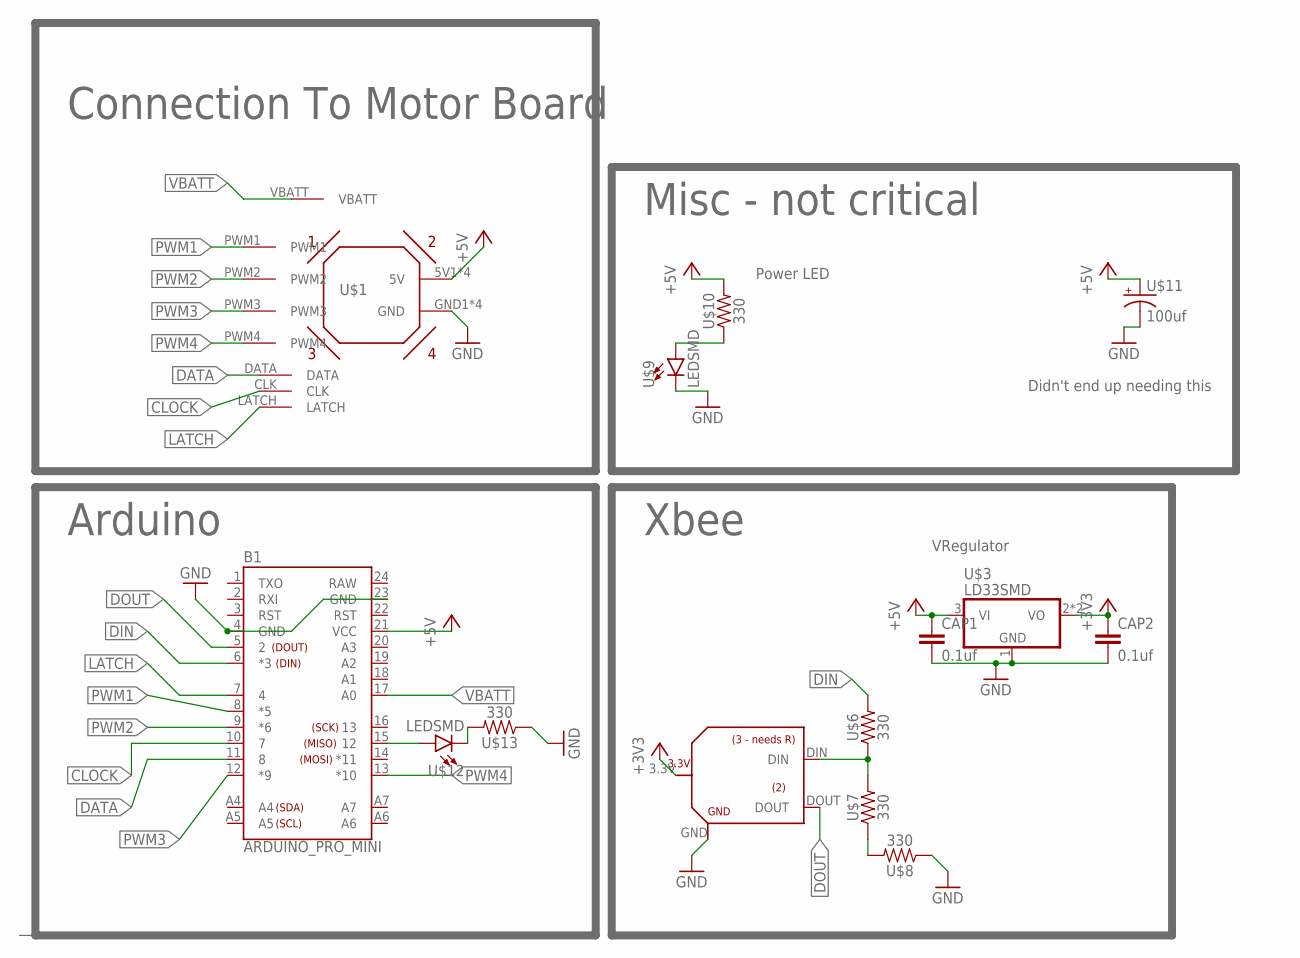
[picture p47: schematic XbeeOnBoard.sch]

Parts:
B1: ARDUINO_PRO_MINI
CAP1, CAP2: 0.1uf; C1206
U$1: OMNIBOARD
U$2: XBEE_BOUT
U$3: LD33SMD; SOT223
U$6, U$7, U$8, U$10, U$13: 330; R1206
U$9, U$12: LEDSMD; LED_SMD
U$11: 100uf; CAP_E

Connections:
+3V3: CAP2.1, U$2.3.3V, U$3.2 (VO), U$3.4 (VO)
+5V: B1.21 (VCC), CAP1.1, U$1.5V1 (5V), U$1.5V2 (5V), U$1.5V3 (5V), U$1.5V4 (5V), U$3.3 (VI), U$10.2, U$11.+
CLOCK: B1.10 (7), U$1.CLK
DATA: B1.11 (8), U$1.DATA
DIN: B1.6 (*3), U$6.2
DOUT: B1.5 (2), U$2.DOUT
GND: B1.4 (GND), B1.23 (GND), CAP1.2, CAP2.2, U$1.GND1 (GND), U$1.GND2 (GND), U$1.GND3 (GND), U$1.GND4 (GND), U$2.GND, U$3.1 (GND), U$8.1, U$9.C, U$11.-, U$13.1
LATCH: B1.7 (4), U$1.LATCH
unnamed: U$9.A, U$10.1
unnamed: B1.15 (12), U$12.A
unnamed: U$7.1, U$8.2
unnamed: U$2.DIN, U$6.1, U$7.2
unnamed: U$12.C, U$13.2
PWM1: B1.8 (*5), U$1.PWM1
PWM2: B1.9 (*6), U$1.PWM2
PWM3: B1.12 (*9), U$1.PWM3
PWM4: B1.13 (*10), U$1.PWM4
RAW: B1.24 (RAW)
VBATT: B1.17 (A0), U$1.VBATT

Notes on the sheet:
Arduino
Xbee
VRegulator
Connection To Motor Board
Misc - not critical
Didn't end up needing this
Power LED

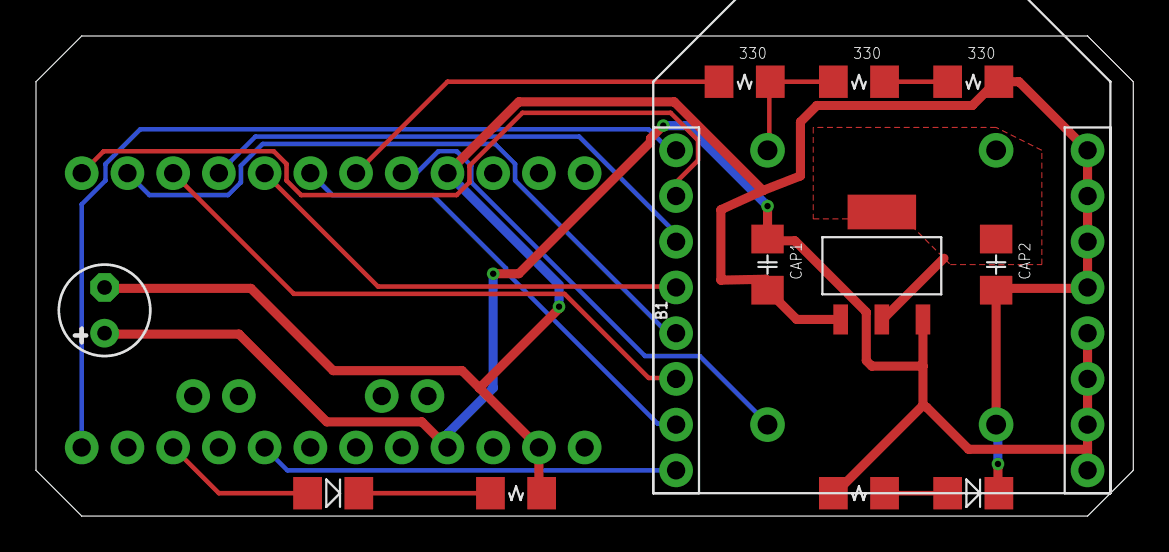
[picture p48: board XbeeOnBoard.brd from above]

Board: 2 copper layers, 61.0 x 26.7 mm, 14 parts (0 on the bottom side), 18 nets.

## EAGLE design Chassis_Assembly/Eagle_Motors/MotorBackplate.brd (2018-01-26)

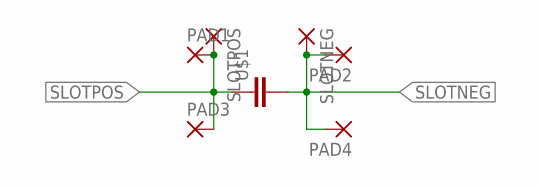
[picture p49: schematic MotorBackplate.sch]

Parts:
PAD1, PAD2: PADNRML; PAD_NRML
PAD3, PAD4: PADLG; PAD_LG
SLOTNEG: PAD; SLOTPAD
SLOTPOS: PAD; SLOTPAD
U$1: CAP_SMNORM; CAP_SM

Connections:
SLOTNEG: PAD2.P$2, PAD4.P$2, SLOTNEG.+, U$1.2
SLOTPOS: PAD1.P$2, PAD3.P$2, SLOTPOS.+, U$1.1

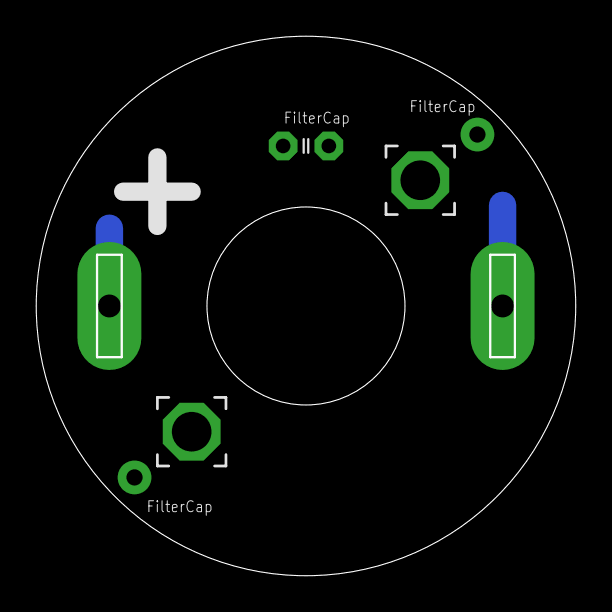
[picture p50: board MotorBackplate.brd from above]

Board: 2 copper layers, 30.0 x 30.0 mm, 7 parts (0 on the bottom side), 2 nets.

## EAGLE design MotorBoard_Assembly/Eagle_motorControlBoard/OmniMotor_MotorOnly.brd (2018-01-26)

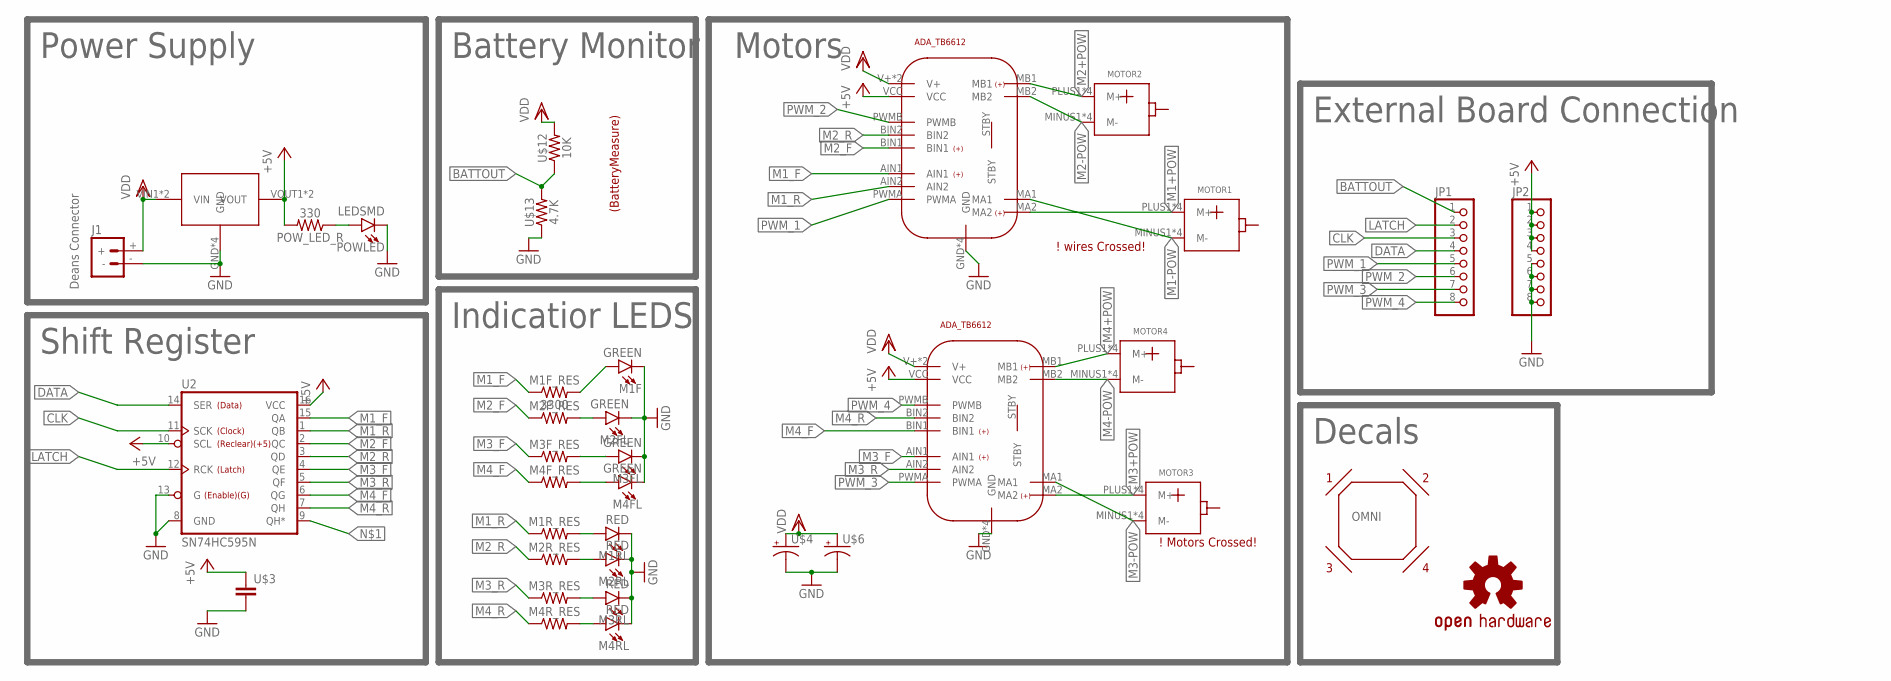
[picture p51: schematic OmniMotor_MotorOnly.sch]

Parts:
J1: BATTERY_CONN_DEANS; DEANS
JP1, JP2: PINHD-1X8BIG; 1X08-BIG
LOGO1: OSHW-LOGOL; OSHW-LOGO-L
M1F, M2FL, M3FL, M4FL: GREEN; LED_SMD
M1F_RES: 3300; R1206
M1RL, M2RL, M3RL, M4RL: RED; LED_SMD
M1R_RES, M2F_RES, M2R_RES, M3F_RES, M3R_RES, M4F_RES, M4R_RES: RESISTORSMD; R1206
MOTOR1, MOTOR2, MOTOR3, MOTOR4: MOTOR_DC
OMNI: OMNI
POWLED: LEDSMD; LED_SMD
POW_LED_R: 330; R1206
U2: SN74HC595N; DIP16
U$1, U$2: ADA_TB6612
U$3: CAP_SMCAP; C1206
U$4, U$6: CAP_EMED; CAP_E
U$5: STEPDOWNGREEN; STEPDOWN
U$12: 10K; R1206
U$13: 4.7K; R1206

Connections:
+5V: JP2.1, JP2.2, JP2.3, JP2.4, POW_LED_R.2, U2.10 (SCL), U2.16 (VCC), U$1.VCC, U$2.VCC, U$3.1, U$5.VOUT1 (VOUT), U$5.VOUT2 (VOUT)
BATTOUT: JP1.1, U$12.1, U$13.2
CLK: JP1.3, U2.11 (SCK)
DATA: JP1.4, U2.14 (SER)
GND: J1.-, JP2.5, JP2.6, JP2.7, JP2.8, M1F.C, M1RL.C, M2FL.C, M2RL.C, M3FL.C, M3RL.C, M4FL.C, M4RL.C, POWLED.C, U2.8 (GND), U2.13 (G), U$1.GND, U$1.GND2 (GND), U$1.GND3 (GND), U$1.GND4 (GND), U$2.GND, U$2.GND2 (GND), U$2.GND3 (GND), U$2.GND4 (GND), U$3.2, U$4.-, U$5.GND, U$5.GND2 (GND), U$5.GND3 (GND), U$5.GND4 (GND), U$6.-, U$13.1
LATCH: JP1.2, U2.12 (RCK)
M1+POW: MOTOR1.PLUS1 (M+), MOTOR1.PLUS2 (M+), MOTOR1.PLUS3 (M+), MOTOR1.PLUS4 (M+), U$1.MA2
M1-POW: MOTOR1.MINUS1 (M-), MOTOR1.MINUS2 (M-), MOTOR1.MINUS3 (M-), MOTOR1.MINUS4 (M-), U$1.MA1
M1_F: M1F_RES.1, U2.15 (QA), U$1.AIN1
M1_R: M1R_RES.1, U2.1 (QB), U$1.AIN2
M2+POW: MOTOR2.PLUS1 (M+), MOTOR2.PLUS2 (M+), MOTOR2.PLUS3 (M+), MOTOR2.PLUS4 (M+), U$1.MB1
M2-POW: MOTOR2.MINUS1 (M-), MOTOR2.MINUS2 (M-), MOTOR2.MINUS3 (M-), MOTOR2.MINUS4 (M-), U$1.MB2
M2_F: M2F_RES.1, U2.2 (QC), U$1.BIN1
M2_R: M2R_RES.1, U2.3 (QD), U$1.BIN2
M3+POW: MOTOR3.PLUS1 (M+), MOTOR3.PLUS2 (M+), MOTOR3.PLUS3 (M+), MOTOR3.PLUS4 (M+), U$2.MA2
M3-POW: MOTOR3.MINUS1 (M-), MOTOR3.MINUS2 (M-), MOTOR3.MINUS3 (M-), MOTOR3.MINUS4 (M-), U$2.MA1
M3_F: M3F_RES.1, U2.4 (QE), U$2.AIN1
M3_R: M3R_RES.1, U2.5 (QF), U$2.AIN2
M4+POW: MOTOR4.PLUS1 (M+), MOTOR4.PLUS2 (M+), MOTOR4.PLUS3 (M+), MOTOR4.PLUS4 (M+), U$2.MB1
M4-POW: MOTOR4.MINUS1 (M-), MOTOR4.MINUS2 (M-), MOTOR4.MINUS3 (M-), MOTOR4.MINUS4 (M-), U$2.MB2
M4_F: M4F_RES.1, U2.6 (QG), U$2.BIN1
M4_R: M4R_RES.1, U2.7 (QH), U$2.BIN2
unnamed: POWLED.A, POW_LED_R.1
unnamed: M1F.A, M1F_RES.2
unnamed: M2FL.A, M2F_RES.2
unnamed: M3FL.A, M3F_RES.2
unnamed: M1RL.A, M1R_RES.2
unnamed: M2RL.A, M2R_RES.2
unnamed: M3RL.A, M3R_RES.2
unnamed: M4RL.A, M4R_RES.2
unnamed: M4FL.A, M4F_RES.2
PWM_1: JP1.5, U$1.PWMA
PWM_2: JP1.6, U$1.PWMB
PWM_3: JP1.7, U$2.PWMA
PWM_4: JP1.8, U$2.PWMB
VDD: J1.+, U$1.V+, U$1.V+2 (V+), U$2.V+, U$2.V+2 (V+), U$4.+, U$5.VIN1 (VIN), U$5.VIN2 (VIN), U$6.+, U$12.2

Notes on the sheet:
Shift Register
Motors
! Motors Crossed!
! wires Crossed!
(BatteryMeasure)
Power Supply
Deans Connector
Indicatior LEDS
Battery Monitor
Decals
External Board Connection

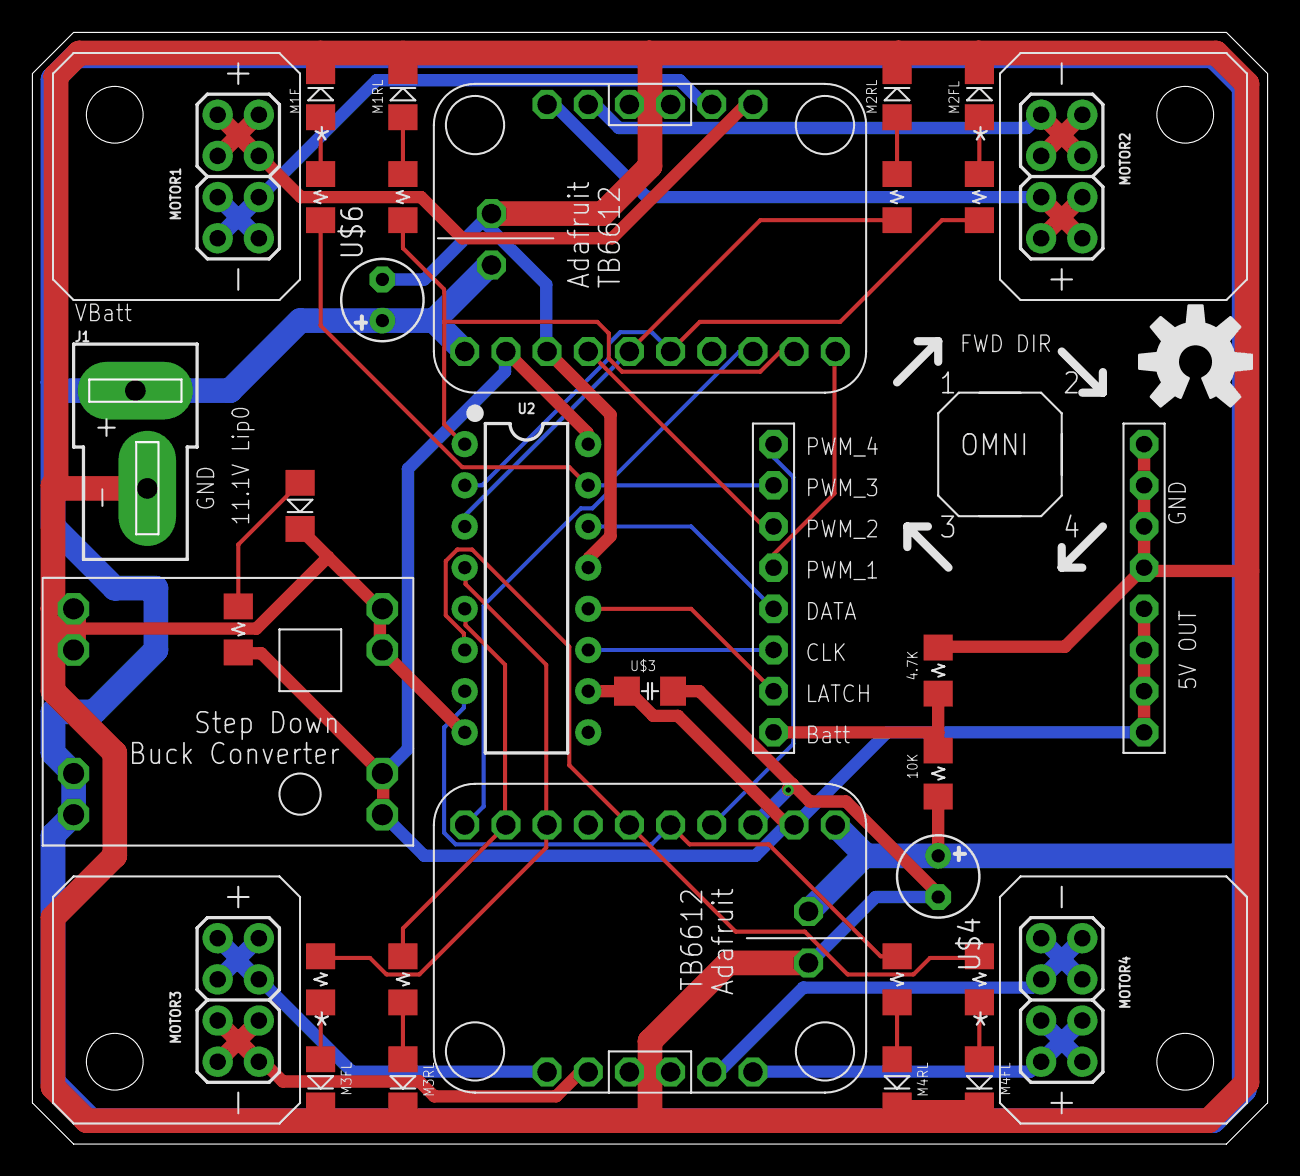
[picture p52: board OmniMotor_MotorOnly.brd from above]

Board: 2 copper layers, 76.2 x 68.6 mm, 36 parts (0 on the bottom side), 36 nets.

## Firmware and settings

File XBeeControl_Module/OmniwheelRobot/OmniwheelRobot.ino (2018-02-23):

// @@@@@@ #include statements to bring in libraries @@@@@@
   #include <SoftwareSerial.h> // for communicating with the XBee
   #include "OmniRobot.h"
   #include "SerialReceiver.h"
// @@@@@@ #define statements for Pin values @@@@@@
   #define SS_RX 2   //RX Pin For Software Serial
   #define SS_TX 3   //TX Pin For Software Serial
   #define PWM_1 5   //
   #define PWM_2 6   //
   #define PWM_3 9   //
   #define PWM_4 10   //

   #define BlueLED 12   //
   #define BatteryV A0   //
   
#define latchPin 4   //Pin connected to latch pin (ST_CP) of 74HC595
#define clockPin 7   //Pin connected to clock pin (SH_CP) of 74HC595
#define dataPin 8   //Pin connected to Data in (DS) of 74HC595

// for communication with remote. hold incoming values.
SoftwareSerial SSConnection(SS_RX,SS_TX); // RX, TX
SerialReceiver mySerialReceiver(&SSConnection);
OmniRobot OmniBot = OmniRobot(PWM_1,PWM_2,PWM_3,PWM_4,latchPin,clockPin,dataPin,BatteryV);

void setup() {
   Serial.begin(9600);
   Serial.println(F("OmniRobotRobot"));
   Serial.println(F("Last Modified 22Feb2018"));
   mySerialReceiver.startReceiver(9600); // change this to 38400 if using bluetooth
// @@@@@@ set mode of output pins @@@@@@
   pinMode(BlueLED,OUTPUT);   //
   OmniBot.welcomeSequence();
   if (OmniBot.getBatteryVoltage() < 6.0) OmniBot.disableLowVolageAlarm(true); // disable low voltage alarm if we are powering over serial port
}

void loop() 
{
  mySerialReceiver.getLatestData(); // get latest data
  movementLoop(); // move robots
}
 

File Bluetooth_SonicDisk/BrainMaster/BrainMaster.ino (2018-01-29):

#include <Wire.h>
#include <stdint.h>

const uint8_t SONIC_DISC_I2C_ADDRESS = 0x09;
#define MOTOR_I2C_ADDRESS 14
#define blinkOutLED 12

const uint8_t NUM_OF_SENSORS = 8; // No. of ultrasonic sensors on SonicDisc
// The packet contains NUM_OF_MEASUREMENTS measurements and an error code
const uint8_t I2C_PACKET_SIZE = NUM_OF_SENSORS + 1;
// The number of measurements from each sensor to filter
const uint8_t MEASUREMENTS_TO_FILTER = 5;
const uint8_t INT_PIN = 2;

// The max valid variance in a set of MEASUREMENTS_TO_FILTER measurements
const unsigned int VARIANCE_THRESHOLD = 3;

// Sonic Disc's operational states
enum State {
  STANDBY, // MCU and sensors are on but no measurements are being made
  MEASURING // Sonic Disc is conducting measurements using the sensors
};

// Values to be received via I2C from master
enum I2C_RECEIPT_CODE {
  STATE_TO_STANDBY = 0x0A,
  STATE_TO_MEASURING = 0x0B
};

// Error codes to be transmitted via I2c to the master
enum I2C_ERROR_CODE {
  NO_ERROR,
  IN_STANDBY,
  INCOMPLETE_MEASUREMENT
};

// Flag to indicate the SonicDisc is ready to send a new set of data
volatile bool newData = false;

uint8_t filterIndex = 0;
uint8_t filterBuffer[MEASUREMENTS_TO_FILTER][NUM_OF_SENSORS] = {0};
uint8_t filteredMeasurements[NUM_OF_SENSORS] = {0};
bool newFilteredMeasurements = false;

boolean UP_BUTTON, DOWN_BUTTON, LEFT_BUTTON, RIGHT_BUTTON,L_TRIG,R_TRIG,JOYSTICK_BUTTON;
int verticalValue = 512, horizontalValue=512;
boolean JoystickBatteryGood;


/**
   Requests an I2C packet from the SonicDisc
   @param  i2cInput         The array that will hold the incoming packet
   @param  transmissionSize The size/length of the incoming packet
   @return                  Error code contained inside the incoming packet
*/
I2C_ERROR_CODE requestPacket(uint8_t i2cInput[], const uint8_t transmissionSize = I2C_PACKET_SIZE) {
  
  Wire.requestFrom(SONIC_DISC_I2C_ADDRESS, transmissionSize);
  uint8_t packetIndex = 0;
  while (Wire.available() && packetIndex < transmissionSize) {
    i2cInput[packetIndex++] = Wire.read();
  }

  return i2cInput[0]; // Return the packet's error code
}


void setup() {
  Wire.begin();
  Serial.begin(38400);
 
  attachInterrupt(digitalPinToInterrupt(INT_PIN), newSonicDiscData, RISING);
  
  Serial.println("Requesting packet from SonicDisc");
  uint8_t dummyInput[I2C_PACKET_SIZE] = {1}; // A throw-away array
 boolean slaveConnected = false;
 
     while(!slaveConnected){
          // Do not proceed unless the SonicDisc is in "MEASURING" state
          sendDataToSonic(STATE_TO_MEASURING);
          
          I2C_ERROR_CODE theErr = requestPacket(dummyInput, I2C_PACKET_SIZE);
          printErrCode(theErr);
          if (theErr == NO_ERROR) slaveConnected = true;
          delay(500);
          Serial.println("Retry connection");
     }
     
 pinMode(blinkOutLED,OUTPUT);
 pinMode(INT_PIN,INPUT);
/*
      while (requestPacket(dummyInput, I2C_PACKET_SIZE) == IN_STANDBY) {
        Serial.println("Setting state to MEASURING");
        sendData(STATE_TO_MEASURING);
      }
*/
  Serial.println("Communication is established and SonicDisc is measuring distances");
}





void loop() {
 // Serial.println(newData);
 delay(10);
 
if (newData) {
    newData = false; // Indicate that we have read the latest data
    digitalWrite(blinkOutLED,HIGH);
    uint8_t sonicDiscInput[I2C_PACKET_SIZE] = {0};
    // Get the I2C packet
    I2C_ERROR_CODE ret = requestPacket(sonicDiscInput, I2C_PACKET_SIZE);
    // Now sonicDiscInput contains the latest measurements from the sensors.
    // However we need to make sure that the data is also of good quality
    // Process the packet only if it is a valid one
    if (ret == NO_ERROR) {
      addInputToFilterBuffer(sonicDiscInput, filterIndex);
      // When we have filled up the filter buffer, time to filter the measurements
      if (filterIndex + 1 == MEASUREMENTS_TO_FILTER) {
        // For each measurement
        sortMeasurements();
        filterMeasurements();
        // Indicate that the measurements are filtered
        newFilteredMeasurements = true;
      }
      // Move along the index
      filterIndex = (filterIndex + 1) % MEASUREMENTS_TO_FILTER;
    }
    digitalWrite(blinkOutLED,LOW);
  }


  if (newFilteredMeasurements) {
    newFilteredMeasurements = false;
    // Print the measurements nicely
    Serial.print("S");
    for (int i = 0; i < NUM_OF_SENSORS; i++) {
      Serial.print(",");
      Serial.print(filteredMeasurements[i]);
    }
    Serial.println(",");
   // digitalWrite(blinkOutLED,LOW);
  }
  

  
  getLatestSerialData();
  directionSelect();
}

void printErrCode(I2C_ERROR_CODE err){

    if(err == NO_ERROR) Serial.println("NO_ERROR");
    if(err == IN_STANDBY) Serial.println("IN_STANDBY");
    if(err == INCOMPLETE_MEASUREMENT) Serial.println("INCOMPLETE_MEASUREMENT");

}


void directionSelect(){
  if( UP_BUTTON) {
  goNorth();
} else if (DOWN_BUTTON) {
  goSouth();
}else if (LEFT_BUTTON) {
  goWest();
}else if (RIGHT_BUTTON) {
  goEast();
}else if (L_TRIG) {
  spinCCW();
}else if (R_TRIG) {
  spinCW();
} else {
  noMov();
}
}



/**
   ISR that raises a flag whenever SonicDisc is ready to transmit new data.
*/
void newSonicDiscData() {
  newData = true;
}

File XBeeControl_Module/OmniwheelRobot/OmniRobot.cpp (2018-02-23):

#include "OmniRobot.h"
#include "Arduino.h"

#define CWSpin 85
#define CCWSpin 170

#define NORTH 153
#define EAST 165
#define SOUTH 102
#define WEST 90

#define NorthEast 129
#define SouthEast 36
#define NorthWest 24
#define SouthWest 66

#define lowVoltageSetting 693 // 11.1 lowV // Low V const precalculated so we're not going the same calculation every loop.
#define R_Batt 10000.0 // not used in code
#define R_GND 4700.0   // not used in code

OmniRobot::OmniRobot(uint8_t PWM1in, uint8_t PWM2in, uint8_t PWM3in, uint8_t PWM4in, uint8_t latchPinIn, uint8_t clockPinIn, uint8_t dataPinIn, uint8_t battVin) {
  OM_PWM1pin = PWM1in;
  OM_PWM2pin = PWM2in;
  OM_PWM3pin = PWM3in;
  OM_PWM4pin = PWM4in;

  OM_latchPin = latchPinIn;
  OM_clockPin = clockPinIn;
  OM_dataPin = dataPinIn;
  OM_battV = battVin;

  // @@@@@@ set mode of output pins @@@@@@
  pinMode(OM_latchPin, OUTPUT);  //
  pinMode(OM_clockPin, OUTPUT);  //
  pinMode(OM_dataPin, OUTPUT);  //

  pinMode(OM_PWM1pin, OUTPUT);  //
  pinMode(OM_PWM2pin, OUTPUT);  //
  pinMode(OM_PWM3pin, OUTPUT);  //
  pinMode(OM_PWM4pin, OUTPUT);  //

  robotSpeed = 160;
  previousDirectionID = 0;
  disableLVA = false;
}

void OmniRobot::welcomeSequence() {
  for (int x = 1; x < 3; x++) // flash the shift register leds a bit to show that we're online.
  {
    sendDataToShiftReg(0);
    delay(250);
    sendDataToShiftReg(255);
    delay(250);
  }
}

void OmniRobot::goNorth() {
  goInDirection(NORTH, 1);
}
void OmniRobot::goSouth() {
  goInDirection(SOUTH, 2);
}
void OmniRobot::goEast() {
  goInDirection(EAST, 3);
}
void OmniRobot::goWest() {
  goInDirection(WEST, 4);
}
void OmniRobot::stopRobot() {
  goInDirection(0, 0);
}

void OmniRobot::rotateCW() {
  goInDirection(CWSpin, 5);
}
void OmniRobot::rotateCCW() {
  goInDirection(CCWSpin, 6);
}

uint8_t OmniRobot::GetRobotSpeed() {
  return robotSpeed;
}
void OmniRobot::SetRobotSpeed(uint8_t newRBTSpeed) {
  robotSpeed = newRBTSpeed;
}

void OmniRobot::disableLowVolageAlarm(boolean activeStatus) {
  disableLVA = activeStatus;
}

float OmniRobot::getBatteryVoltage() {
  int theRead = analogRead(OM_battV);
  float divRatio = (R_Batt + R_GND) / R_GND;
  float vPinLoc =  5.0 * float(theRead) / 1023.0;
  return divRatio * vPinLoc;
}

boolean OmniRobot::batterySafeVoltage()
{
  return (analogRead(OM_battV) > lowVoltageSetting);
}

void OmniRobot::lowVoltageAlarm() // if the main battery is bad, alert the user and stop.
{
  if (disableLVA) return;
  digitalWrite(OM_PWM1pin, 0);
  digitalWrite(OM_PWM2pin, 0);
  digitalWrite(OM_PWM3pin, 0);
  digitalWrite(OM_PWM4pin, 0);
  // make cool looping thingy with LEDS to show low battery (robot)
  while (1) {

    sendDataToShiftReg(1);
    delay(200);
    sendDataToShiftReg(2);
    delay(200);
    sendDataToShiftReg(4);
    delay(200);
    sendDataToShiftReg(8);
    delay(200);
    sendDataToShiftReg(16);
    delay(200);
    sendDataToShiftReg(32);
    delay(200);
    sendDataToShiftReg(64);
    delay(200);
    sendDataToShiftReg(128);
    delay(200);
  }
}

/*
  float dividerRatio()
  {
  return (R_Batt + R_GND) /R_GND ;
  }
*/

void OmniRobot::goInDirection(int theDirection, int currentDirectionID)
{
  if (!batterySafeVoltage()) lowVoltageAlarm();
  if ((theDirection != 0) && (currentDirectionID == previousDirectionID)) {
    analogWrite(OM_PWM1pin, robotSpeed);
    analogWrite(OM_PWM2pin, robotSpeed);
    analogWrite(OM_PWM3pin, robotSpeed);
    analogWrite(OM_PWM4pin, robotSpeed);
  } else {
    analogWrite(OM_PWM1pin, 0);
    analogWrite(OM_PWM2pin, 0);
    analogWrite(OM_PWM3pin, 0);
    analogWrite(OM_PWM4pin, 0);
  }
  this->sendDataToShiftReg(theDirection);
  delay(25);
  if (currentDirectionID != previousDirectionID) delay(50);
  previousDirectionID = currentDirectionID;
}

void OmniRobot::sendDataToShiftReg(int z) //generic code for controlling shift register
{
  shiftOut(OM_dataPin, OM_clockPin, MSBFIRST, z);
  digitalWrite(OM_latchPin, HIGH);
  delay(1);
  digitalWrite(OM_latchPin, LOW);
}

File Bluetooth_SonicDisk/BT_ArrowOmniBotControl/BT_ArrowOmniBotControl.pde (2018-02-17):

import processing.serial.*;
SerialConnector sc;
Serial myPort;

SonicDisc SD;

boolean UP_BUTTON, DOWN_BUTTON, LEFT_BUTTON, RIGHT_BUTTON,L_TRIG,R_TRIG;
boolean SPD_H,SPD_M,SPD_L;

int sonic0 = 30;
int sonic1 = 30;
int sonic2 = 30;
int sonic3 = 30;

int sonic4 = 30;
int sonic5 = 30;
int sonic6 = 30;
int sonic7 = 30;

void setup(){
 size(1800,1000);
 
 sc = new SerialConnector(this,myPort);
 SD = new SonicDisc();
 sc.changeBaud(38400);
 
  rectMode(CENTER);
  sc.listPorts();
}

void draw(){
  if (sc.isConnected){
     background(50,60,50); 
  } else {
     background(60,50,50);       
  }
  
  /*
 *  7: always 0
 *  6: Joystick button state
 *  5: Left Trigger State
 *  4: Right trigger state
 *  3: up button state
 *  2: down button state
 *  1: left button state
 *  0: right button state
*/
  //packageSent = false;
  SD.drawSonicRing(sonic0,sonic1,sonic2,sonic3,sonic4,sonic5,sonic6,sonic7);
  sc.drawToScreen();
  
  if (keyPressed) {
  
    if (UP_BUTTON) sendPackage(customByte(false,false,false,false,true,false,false,false));
    if (LEFT_BUTTON) sendPackage(customByte(false,false,false,false,false,false,true,false));
    if (DOWN_BUTTON) sendPackage(customByte(false,false,false,false,false,true,false,false)); 
    if (RIGHT_BUTTON) sendPackage(customByte(false,false,false,false,false,false,false,true));
    if (L_TRIG) sendPackage(customByte(false,false,true,false,false,false,false,false));
    if (R_TRIG) sendPackage(customByte(false,false,false,true,false,false,false,false)); 
        
     if (SPD_H) sendPackage(customByte(true,true,false,false,false,false,false,false));
     if (SPD_M) sendPackage(customByte(true,false,true,false,false,false,false,false));
     if (SPD_L) sendPackage(customByte(true,false,false,true,false,false,false,false));
    
    
    delay(10);
  } else { 
    sendPackage(customByte(false,false,false,false,false,false,false,false)); 
    resetButtons();
  }
  
}

void keyPressed() {
  sc.KeyInputforConnection(key);

  if (key == 'q') {L_TRIG = true;} else {L_TRIG = false;}
  if (key == 'e') {R_TRIG = true;} else {R_TRIG = false;}
  if (key == 'w') {UP_BUTTON = true;} else {UP_BUTTON = false;}
  if (key == 's') {DOWN_BUTTON = true;} else {DOWN_BUTTON = false;}
  if (key == 'a') {LEFT_BUTTON = true;} else {LEFT_BUTTON = false;}
  if (key == 'd') {RIGHT_BUTTON = true;} else {RIGHT_BUTTON = false;}

   if (key == 'j') {SPD_H = true;} else {SPD_H = false;}
   if (key == 'k') {SPD_M = true;} else {SPD_M = false;}
   if (key == 'l') {SPD_L = true;} else {SPD_L = false;}

}



/*

  if (isSet(aByte,7)){   // unpack joystick & batteries

  //  byte H_val = customByte(false,false,false,false,false,isSet(aByte,5),isSet(aByte,4),isSet(aByte,3));
  //  byte V_val = customByte(false,false,false,false,false,isSet(aByte,2),isSet(aByte,1),isSet(aByte,0));
  //  JoystickBatteryGood = isSet(aByte,6);
  //  horizontalValue = unpackJoystick(H_val);
  //  verticalValue = unpackJoystick(V_val);

  if (isSet(aByte,6)) OmniBot.SetRobotSpeed(225);
  if (isSet(aByte,5)) OmniBot.SetRobotSpeed(160);
  if (isSet(aByte,4)) OmniBot.SetRobotSpeed(120);
  
  }

*/



void sendPackage(byte aByte){
     sc.writeToSerial(aByte);
     sc.writeToSerial(-31);
}


void resetButtons(){
  UP_BUTTON = false;
  DOWN_BUTTON = false;
  LEFT_BUTTON = false;
  RIGHT_BUTTON = false;
  L_TRIG = false;
  R_TRIG = false;
  
}

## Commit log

2018-01-21 update readme by adding eagle links, total replacement of code with new version
    [MovementControl.ino, OmniRobot.cpp, OmniwheelRobot_Xbee.ino]
2018-01-26 Add eagle PCB files for Motor Control Board
    Add eagle PCB files for Motor Control Board
    [OmniMotor_MotorOnly.brd, OmniMotor_MotorOnly.sch]
2018-01-26 Add eagle PCB files
    Add eagle PCB files for Motor backplate and attachment
    [MotorBackplate.brd, MotorBackplate.sch, MotorBoard.brd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]
2018-01-28 Add DXF files for laser cutting
    these files can be used to laser cut the upper and lower plates. open in mm.
    [LowerPlate.dxf, UpperPlate.dxf]
2018-01-28 add 3D Printable STL Files
    STL files for 3D Printing
    [BatteryHolderA_2.stl, BatteryHolderB_2.stl, MotorHolderE.stl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]
2018-02-01 Update README.md
    add link to wireless joystick code
2018-02-01 xbee board
2018-02-01 update xbee board
2018-02-01 add eagle files
    add eagle files
    [I2CSlave_OnBoard.brd, I2CSlave_OnBoard.sch]
2018-02-04 add eagle PCB
    [BrainControlBoard.brd, BrainControlBoard.sch]
2018-02-05 update PDF instructions, update readme's, rename some code
    [BrainControlBoard.brd, BrainControlBoard.sch]

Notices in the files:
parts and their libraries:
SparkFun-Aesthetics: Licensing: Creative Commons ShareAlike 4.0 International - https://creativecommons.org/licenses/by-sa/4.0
